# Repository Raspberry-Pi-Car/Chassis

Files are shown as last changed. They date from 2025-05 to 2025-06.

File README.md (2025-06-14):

# PiCar Chassis
A 3D printable chassis for a 2-wheel drive Raspberry Pi controlled car designed for personal and academic use.

## OnShape Model

A revised model (01/06/2025) can be found at: [PiCarChassis2](https://cad.onshape.com/documents/606afa32c4ddef82647d70d7/w/6173d1c845c871eaac10e766/e/4a1e5e404db76d444ffd6e8d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)

## 3D printing

For those who do not want to customize their car in any way, the STL files are available in **V1-STLs**. These STL files have no fun names embedded in the print and are designed to be as simple as possible. Please note, the parts title ***Print2*** will need two of these item printed to be able to completely assemble the car. These parts are the _Front Shaft Spacer_, _Front Shaft_, _N20 Sleeve_, and _Rear Spacer_. All other items in the print only need a single copy per car. 

For **V2-STLs**, the number at the end, ie. the `#` in `NAME-#.stl`, is the number of parts that need to be printed.

Happy printing!!

### Custom text printing

The text on the car can be edited by opening the _Chassis_ tab and scrolling down to the folder _TEXT (2)_ and editing the two sketches that are inside (`TEXT TOP` & `TEXT BOTTOM`). Once in the sketch, right-click on the text itself and you can modify the name and number. You can remove the text by right-clicking on the extrusions (`Extrude Text Top` & `Extrude Text Bottom`) and selecting _suppress_.

Video tutorial will be added soon<sup>TM</sup>.

## Required Hardware

Below is a list of hardware that is used to assemble the design and links to get them from different suppliers.

| Part and Model | Quantity | Purchase Link 1 | Purchase Link 2 | Purchase Link 3 |
| --- | --- | --- | --- | --- |
| N20 Motors (6V 300 to 400 RPM recommended) | 2 | [AliExpress](https://www.aliexpress.us) | [Alibaba](https://www.alibaba.com) | [Amazon](https://a.co/d/13G6bXz) |
| MF148ZZ Bearing (8x14x4mm) | 10 | [AliExpress](https://www.aliexpress.us)  | [Alibaba](https://www.alibaba.com) |
| 12mm Hex to 8mm Wheel Coupling | 4 | [AliExpress](https://www.aliexpress.us) | [Alibaba](https://www.alibaba.com)
| PiCamera (v1 fit tested, v2 untested) | 1 | 
| Ultrasonic Sensor | 1 | 

The screws and other hardware can be bought as individual kits from Amazon/AliExpress/Alibaba or as individual parts at McMaster-Carr or you local hardware store. 

| Hardware Size | Type | Quantity | Purpose | Note |
| --- | --- | --- | --- | ---|
| M1.6 x 8mm Machine Screws (Can be plastic) | Pan head or Countersunk | 8 | Camera and Ultrasonic Sensor | Working to remove this requirement |
| M2 x 10/12mm Machine Screws | Pan head or Countersunk | 6 | Servos mounting |
| M2 Nuts | | 6 | With M2 Screws |
| M3 x 10mm Machine Screws | Pan head or Countersunk | 9 | Chassis and Head Stabilization |
| M3 x 8 or 10mm Machine Screws | Countersunk | 2 | Battery Holder | 
| M3 Nuts | | 3 | Battery Holder and Head Stabilization |
| M3 Heat Insert | One Sided | 8 | Chassis |
| M4 x 8mm Machine Screw | Pan Head | 4 | Wheel Coupling |
| | | | |
| M1.7 Self-tapping Screws | Comes with servos | 4-5 | For Servo Arms | 

## How to assemble

Assembly tutorial Coming Soon<sup>TM</sup>.

## Purpose 
### Motivation
After taking ESE 205, _Introduction to Engineering Design_ course at Washington University in St. Louis, and later becoming an _Assistant Instructor_ for the course, I needed to repair the commercial alternative. The brand will not be stated, but the vehicles were extremely time-consuming to construct and more importantly to maintain in a class setting. The servos were continuously getting stripped and needing continuous replacement. The was due to the weight of the items being supported, the nature of first year students, and the design being made of laser cut polycarbonate. This meant that the full car is held together with a lot of screws and hardware Which can be avoided if 3D printing is used. 

Since the big boom of 3D printing, 3D printing is more available than ever, it made sense to try and remake the cars using 3D printing, allowing for easier maintenance, since if a part broke, it could easily be reprinted. If the requirements for the class change, the model can be updated and reprinted for ~$5. The goal was to use less hardware as well, dropping the screw requirement from approximately 50 down to approximately 20 and removing the need for M3 standoffs to connect two laser cut panels together.  

### Goal
The goal was to design a simple and complete design for use in an introductory level hardware interfacing class. The goal of the class was to use onboard sensors to complete specified tasks as set by the instructor of the course. The chassis was to be design to be easy to assemble, easy to print, and, most importantly, easy to maintain. The aim was to make the servos easily replaceable while stabilizing the head and removing steering slop, which were both problems on the original design. 

### Overall Model

PiCar Model

### Current Model

The current model is made with OnShape, the goal is to soon release another model that uses Fusion360 to allow for more choices for individuals looking to customizing their own car.

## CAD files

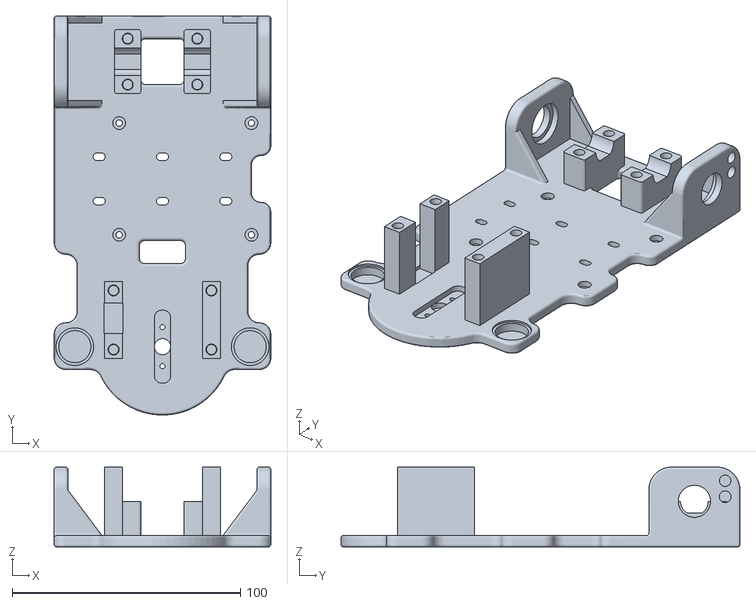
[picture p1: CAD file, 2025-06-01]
V2-STLs/Main Body-1.stl
95.0 x 175.0 x 35.0

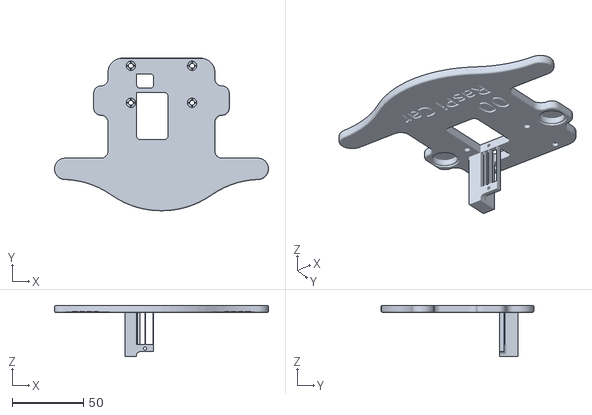
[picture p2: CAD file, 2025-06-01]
V2-STLs/Front Body-1.stl
149.9 x 106.9 x 36.0

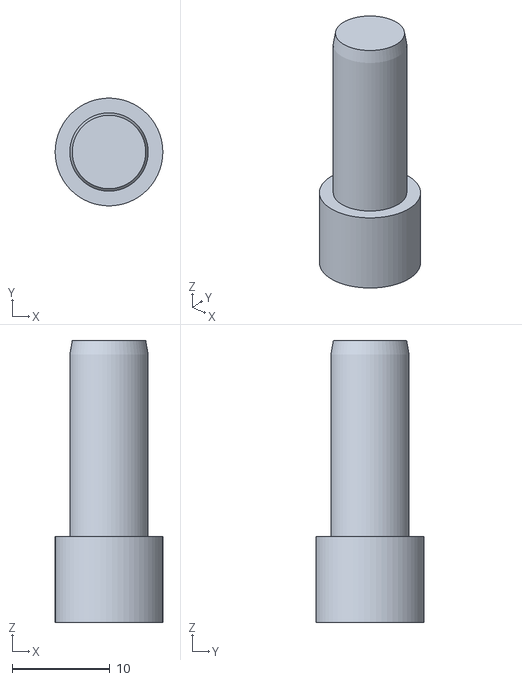
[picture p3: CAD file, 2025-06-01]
V2-STLs/N20 Shaft-2.stl
11.0 x 11.0 x 28.8

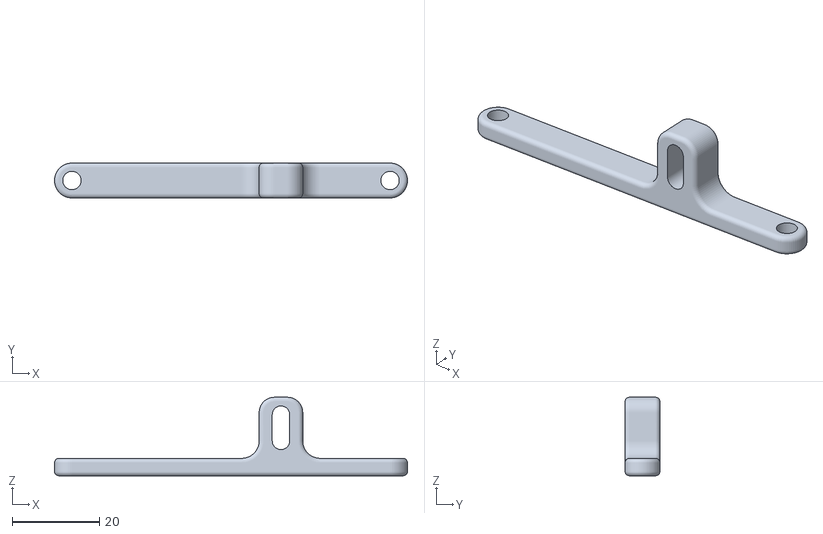
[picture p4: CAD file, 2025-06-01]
V2-STLs/Steering Arm-1.stl
80.9 x 8.00 x 18.0

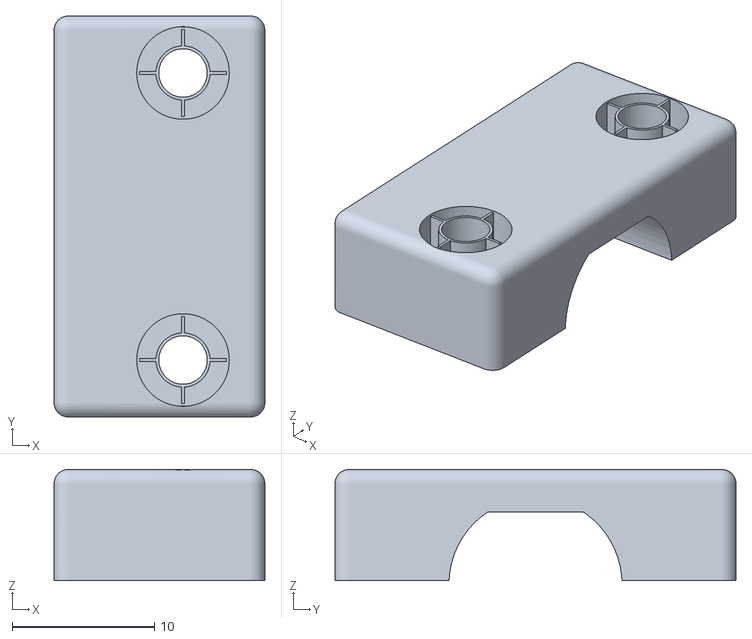
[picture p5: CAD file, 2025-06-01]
V2-STLs/MountTopL-1.stl
14.8 x 28.1 x 7.80

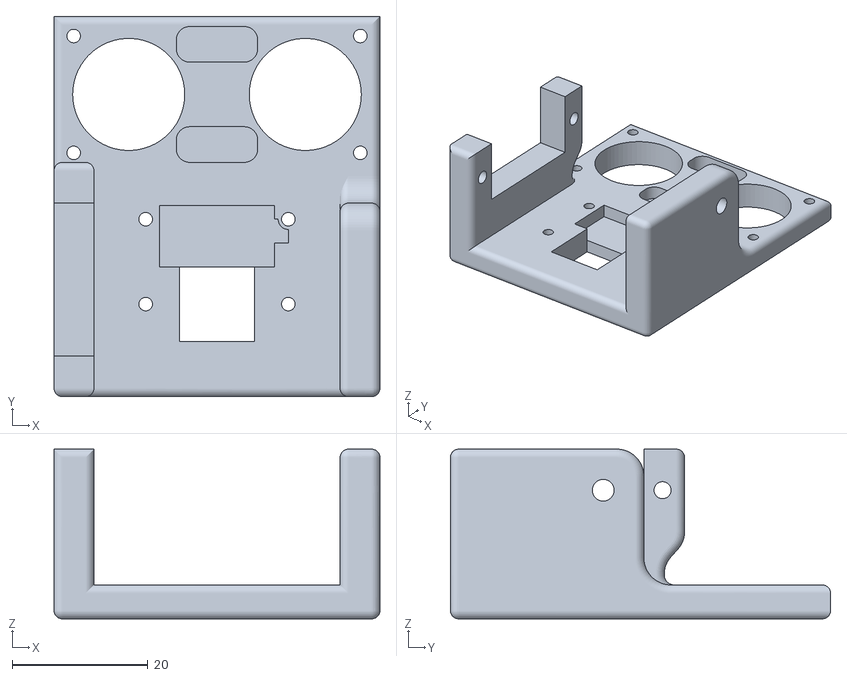
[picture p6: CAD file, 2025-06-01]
V2-STLs/HeadV2-1.stl
48.0 x 56.0 x 25.0

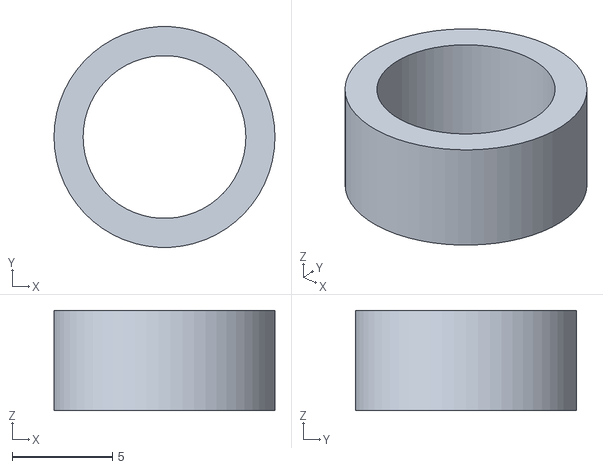
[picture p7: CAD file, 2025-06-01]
V2-STLs/Rear Spacer-2.stl
11.0 x 11.0 x 5.00

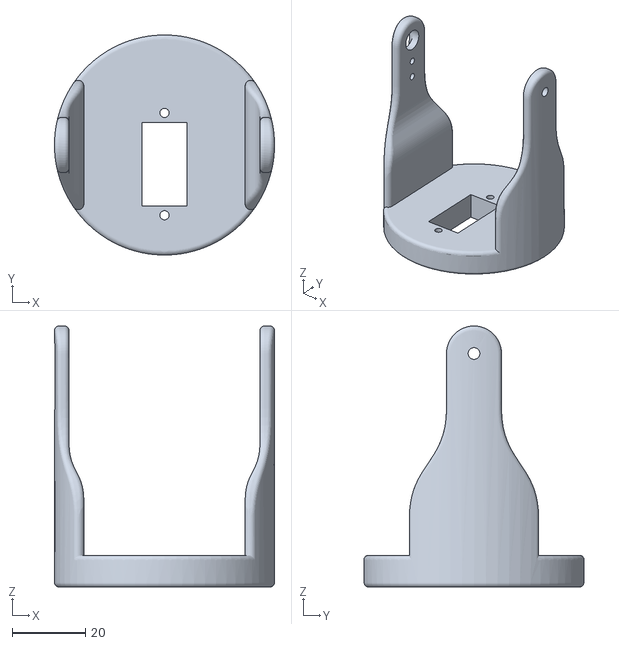
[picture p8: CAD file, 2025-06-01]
V2-STLs/HeadBaseV2-1.stl
60.0 x 60.0 x 71.1

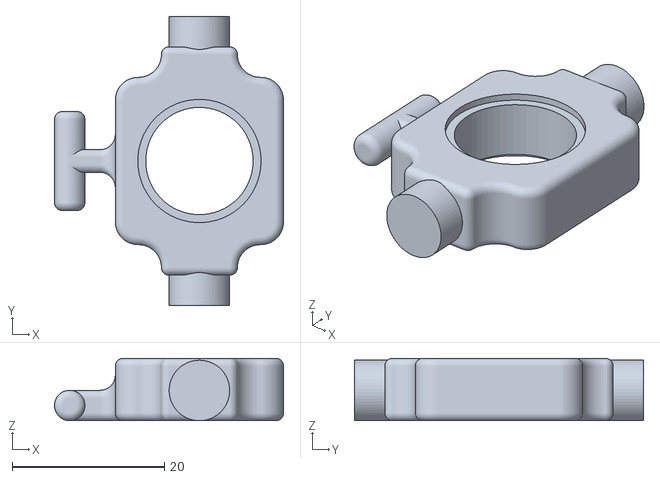
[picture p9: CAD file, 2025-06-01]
V2-STLs/Bearing Hub V2-2.stl
30.1 x 38.0 x 8.20

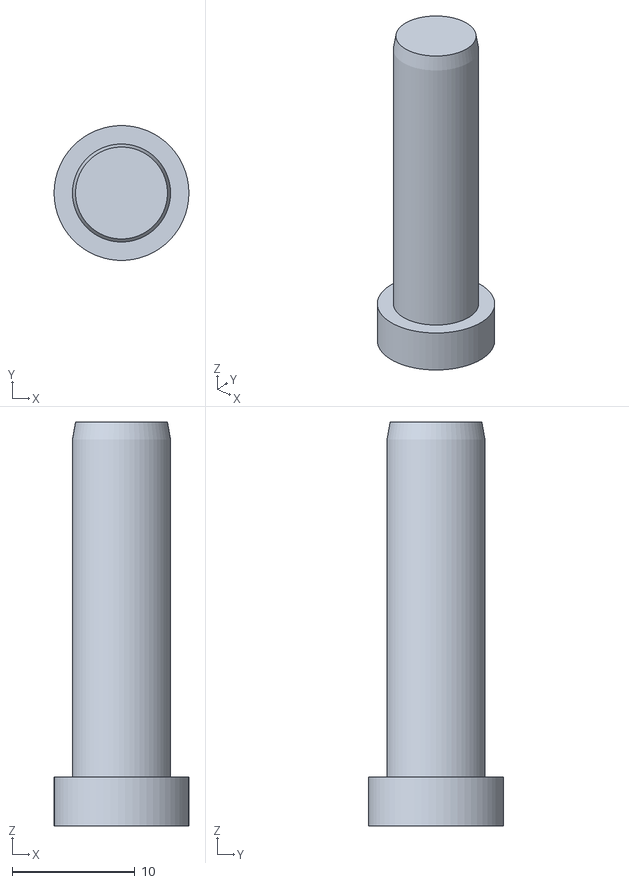
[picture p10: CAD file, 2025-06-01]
V2-STLs/Front Shaft-2.stl
11.0 x 11.0 x 33.0

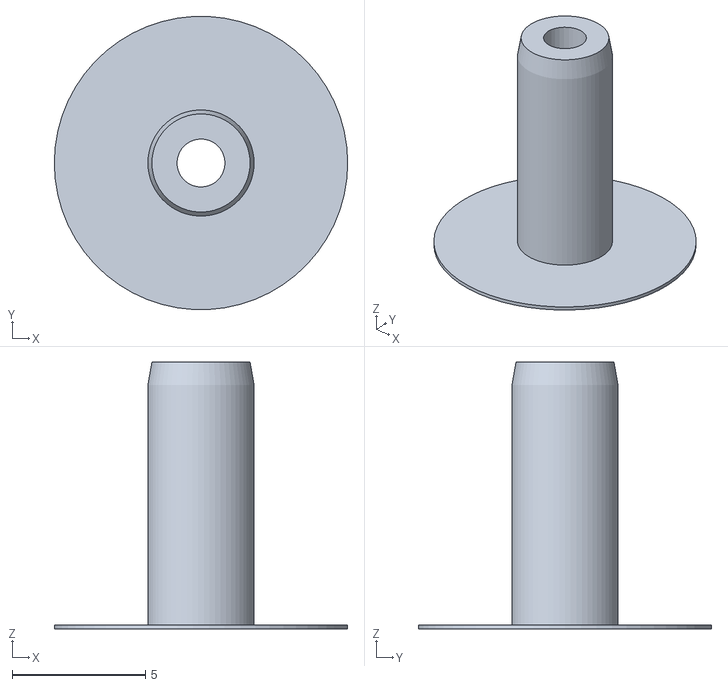
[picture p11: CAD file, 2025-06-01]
V2-STLs/Steer Shaft-1.stl
11.0 x 11.0 x 10.0

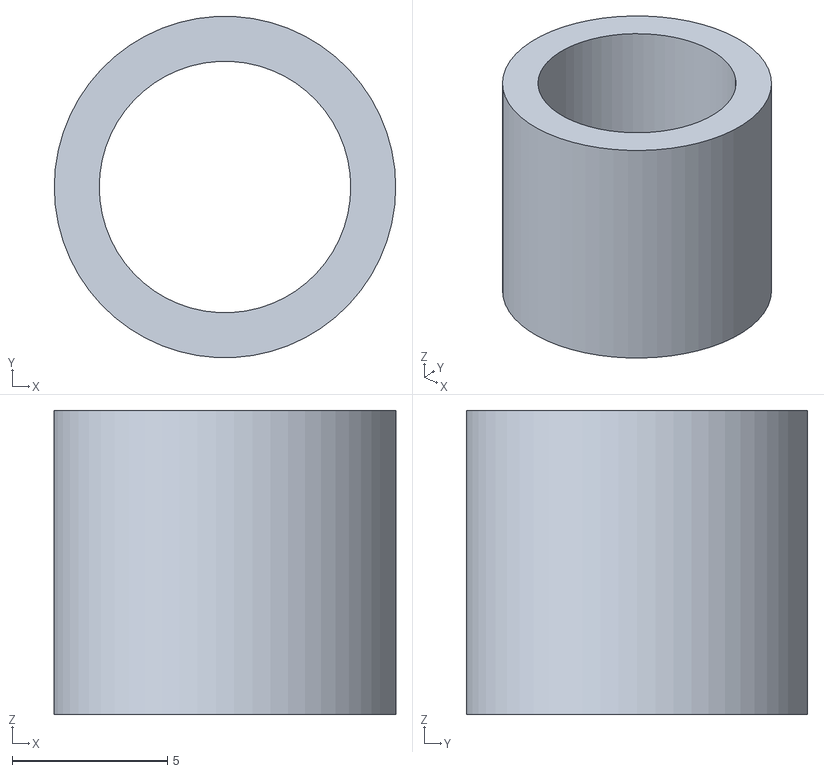
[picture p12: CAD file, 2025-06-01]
V2-STLs/Front Spacer-2.stl
11.0 x 11.0 x 9.80

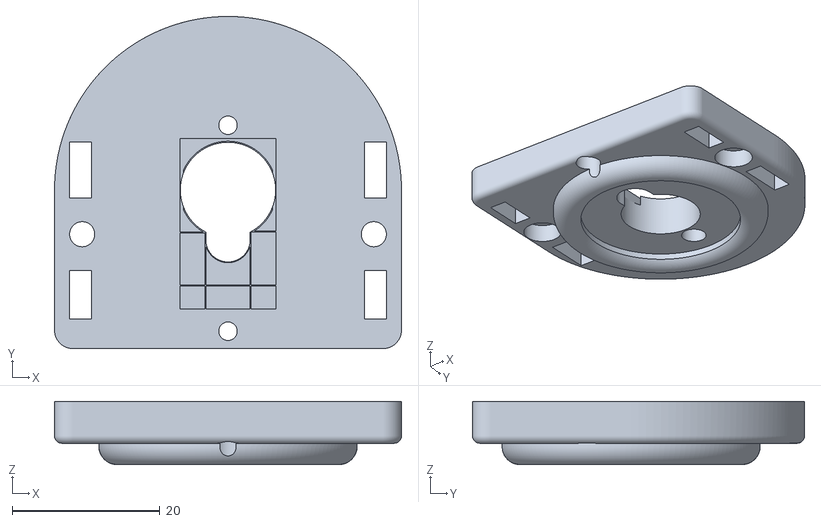
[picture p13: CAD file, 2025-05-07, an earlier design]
V1-STLs/Print - Head Base.stl
47.0 x 45.0 x 8.58

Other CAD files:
V2-STLs/MotorTopR-1.stl
V1-STLs/Print2 - N20 Sleeve.stl
V1-STLs/Print2 - Front Shaft Spacer.stl
V1-STLs/Print - Steering Arm.stl
V1-STLs/Print2 - Rear Spacer.stl
V1-STLs/Print - Bearing Hub L.stl
V1-STLs/Print - Bearing Hub R.stl
V1-STLs/Print - Head Side L.stl
V1-STLs/Print - Head Side R.stl
V1-STLs/Print - MotorTopR.stl
V1-STLs/Print - MountTopL.stl
V1-STLs/Print - Servo Extention.stl
V1-STLs/Print - The Head.stl
V1-STLs/Print2 - Front Shaft.stl

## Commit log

2025-05-07 Added parts list and STL files for M3 insert model as V1-STLs
    [Print - Bearing Hub L.stl, Print - Bearing Hub R.stl, Print - Head Base.stl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]
2025-06-01 Minor modification to the text in Readme.m and added V2 stls
    [Bearing Hub V2-2.stl, Front Body-1.stl, Front Shaft-2.stl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]
